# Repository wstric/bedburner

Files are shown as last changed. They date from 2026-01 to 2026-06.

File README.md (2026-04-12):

# PTC Heated bed fans mod for Voron 2.4 Printers
Spicy _bed_ fan mod with an "after _burner_" -> BedBurner.

Installed on Voron 2.4 bed rails. Can be placed on the outside, center or both.

Outer placement will be covered by the bed for 300 and 350 size but exposed on 250 size.

Requires raising the bed for clearance and to prevent damage to the bed heater.
Mods like Whoppingpochard kinematic bed mount do this with other benefits.

:fire: :fire: :fire:

> [!CAUTION]
> Installation of this mod involves wiring mains AC voltage and addition of heaters without thermistor feedback.
>
> Careful wiring and component selection can reduce the risk of injury or fire,
> but only similar to the existing components of a v2.4 but never zero.
>
> This mod should not be attempted without experience and caution.
> I am not responsible for any resulting damage or harm.

> [!Warning]
> Do NOT ask about this mod in the Voron Design Discord.

:fire: :fire: :fire:

## Design

The goal of this mod was to create a minium height chamber heater for the Voron V2.4 that
could slip into the unused space under the bed and provide enough thermal output to match
the extruder. This would allow the printer to more easily heatsoak at the same temperatures
that would be reached during printing. More active chamber temperature control was a bonus
and a slight increase in temperatures was welcome. Other heaters setups can be off-the-shelf
and more off-the-shelf and provide much more power. However, they were simply too bulky
and had to mounted in the open or be in the way of existing components.

After much research and trying to make hotend cartridge heater work I found the aluminum shell
PTC heater form factor. While lacking in surface area it is very compact, electrically isolated
and could be easily mounted heatsink. Balancing space, thermal out, and availability lead to
35mm x 20mm x 5mm nominal size PTC and 50mm x 50mm x 20mm heatsink. This left enough space for
safety features such as a thermal switch as a fail safe and further cap the maximum temperature.

Modifying the off the shelf heatsink ending up being one of the most challenging part. While
the steel brackets (metal for safety in the worst case, and steel for poor conductivity) would
have been impossible to make myself they were easy to outsource to services like SendCutSend.
The modified heatsink would have been prohibitive to outsource machined from raw stock and
a struggle to do with hand tools. There were easier ways to mount but was decided that retaining
components in pockets strapped in with screws was necessary for safety.

The resulting setup ended being a little too tall for a stock V2.4 bed spacers. This wasn't an
issue since the Whooping kinematic bed mod already gave plenty of height. Using 5015 radial
blower fan and matching ducts; two units could be fit in between the bed extrusions and
another two could be hidden under a 300mm or 350mm bed on the outside.

### Results
* Twin BedBurner test rig setup:
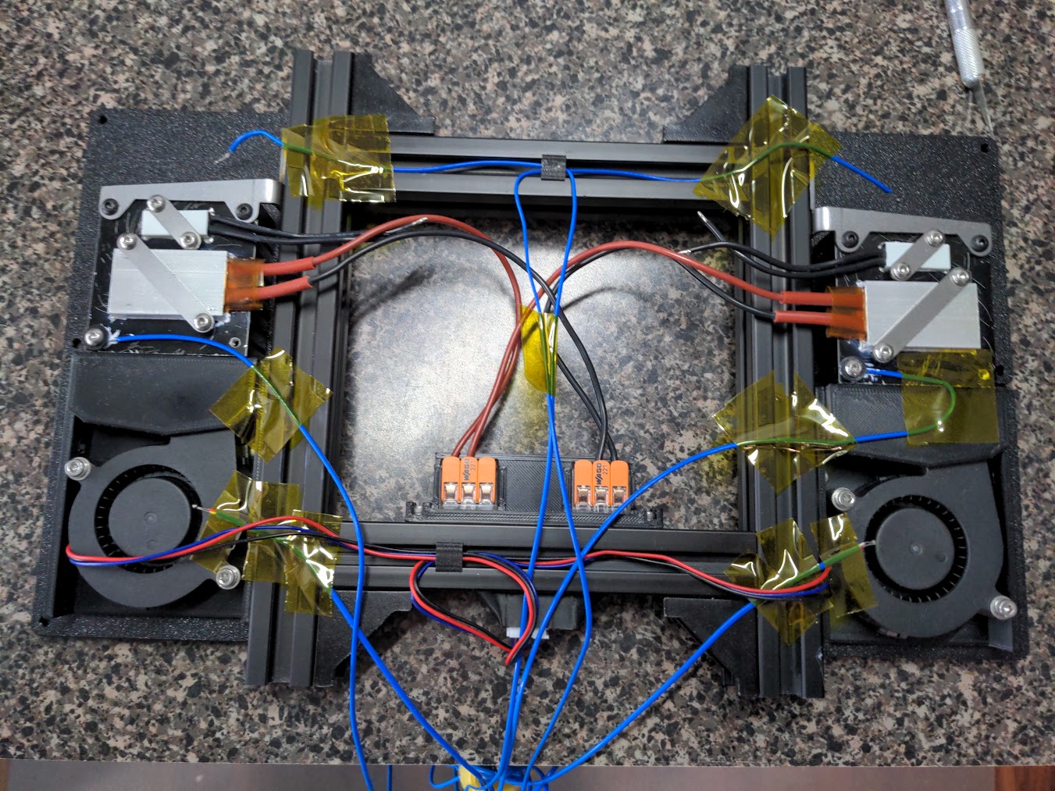
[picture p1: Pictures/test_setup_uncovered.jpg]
test_setup_uncovered
  * 
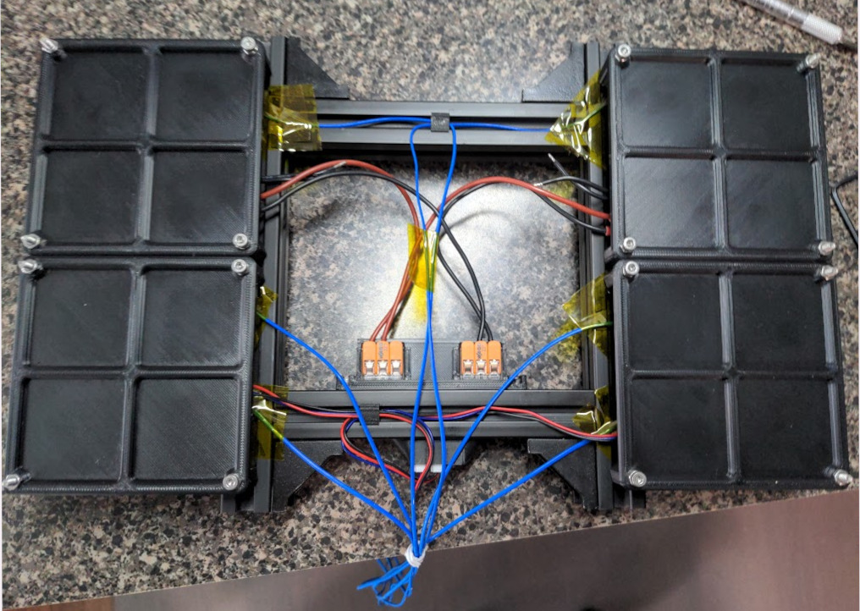
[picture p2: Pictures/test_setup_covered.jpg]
  * 
  * Thermocouples were placed at the fan intake, on the block surface and at the block exhaust.
  * Combined amperage was measured and recorded along with temperature readings.
  * was inside an thinly insulated box with a simulated V2.4 configuration.
  * Heaters output over 70 watts each at 25C ambient.
  * The block surface peaked at rough 80C in 25C ambient.
  * Output dropped to roughly 60 watts each at 75C ambient.
* Twin BedBurner setup installed in a v2.4 300:
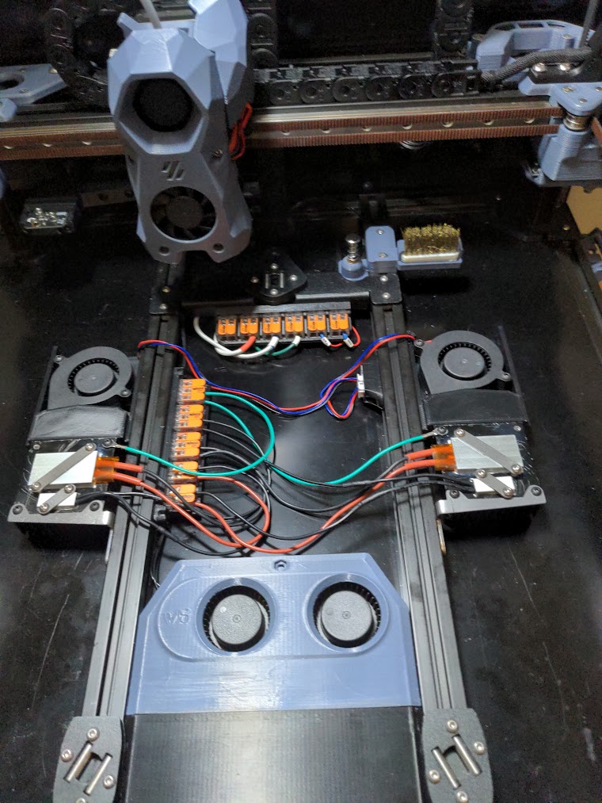
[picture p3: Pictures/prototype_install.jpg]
prototype_install
  * 
  * Stock panels and doors, stock exhaust, no blanket or insulation.
  * Nevermore micro v6 recirculating and exaust fan off.
  * Heatsoaking bed at 105C and 100% BedBurner.
  * Chamber temperature reached stable 65C. 
  * Measured at gantry rear extrusion with toolhead centered and 120mm over bed

## Parts List
* Machined heater block
* Cut and bent bracket and straps
* PTC heater
* thermal failsafe (thermal switch / thermal fuse / thermistor)
* 5015 radial (blower) fan
* 3D printed fan duct
* Assorted M3 hardware

### [Detailed BOM](./README_bom.md)

## Instructions

### [Fabrication](./README_fabrication.md)

### [Assembly](./README_assembly.md)

### [Configuration](./README_config.md)

---

Special thanks to the Fabreeko discord and Delmar for tolerating these shenanigans.

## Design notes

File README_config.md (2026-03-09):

# BedBurner Software Configuration

Klipper does not make chamber heaters easy.
They are, in effect, modeled as bed heaters which causes complications in most configurations.
The two main paths for configuring are to work around the Klipper or implement custom control.

## Klipper Control Solution

Klipper control gets hacky, but has the advantage of being controlled in real time.
It is always running and will not be blocked by the command queue.
The macro is also much easier to understand even if what is can do is narrow.
The only real downside it you are working around the limitations and opinions of Klipper.
Depending on your setup this might be no downside at all.

Some limitations you might need to work around include:
  * Heaters can only be controlled by a temperature sensor
  * Using verify_heater is impossible using the chamber temp. No safety for you.
  * Nether heater_fan or controller_fan can cycle off except during cool down.
  * If you have one chamber termistor, duplicate pin validation.

Provided example was extensively tested in Kalico v0.12 and provides control of
chamber heater & fan, filter and exhaust.

#### [klipper control example config](/Firmware/klipper/klipper_control)

## Custom Control Solution
Custom control gives a lot of freedom to customize how it behaves.
I have implemented my own version using delayed_gcode which makes it simple to implement,
but comes with the limitation that it can be interrupted temporally by long running commands
(like a typical print start macro).

The configuration is simple configuration and can model the filter, exhaust, heater fan
and heater element as `fan_generic` so that a macro may control without Klipper stepping in.
Practically, you are limited to watermark (aka bang-bang) control in a custom macro,
but this is quite suitable for chamber temperature regulation.

Provided example was extensively tested in Klipper v0.12 and provides control of
chamber heater & fan, filter and exhaust.

#### [custom control example config](/Firmware/klipper/custom_control)

---

For examples given above chamber temperature control is abstracted by `HEAT_CHAMBER` and `COOL_CHAMBER` macros.
The `HEAT_CHAMBER` should be called in your print start (and heatsoak if you have one) macros.
`COOL_CHAMBER` should be called in your print end macro.

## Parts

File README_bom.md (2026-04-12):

# BedBurner Detailed BOM

## Common Components 
* Heater block
  * Heatsink - 50mm x 50mm x 20mm
  * Machined with component pockets and tapped holes
  * Variant of block should match the thermal fail-safe option selected
  * Detailed instructions in [fabrication section](./README_fabrication.md#Heater-Heatsink)

* Mouting bracket
  * Cut and bend from 16ga mild steel
  * Requires front, rear or both brackets
    * Rear bracket least compact but accessible screws makes easier to install and service
    * Front bracket covers extrusion screws and makes hard to align
    * Can use both front and rear brackets for extra sturdy mounting
  * STEP models and DXF files are provided
  * Detailed instructions in [fabrication section](./README_fabrication.md#Heater-Bracket)

* PTC heater
  * Aluminum shell PTC heater
  * Nominal size 35mm x 20mm x 5mm size
  * Quality control is loose so test current draw and max temp before usage

* PTC component strap
  * Cut from 22ga mild steel
  * Detailed instructions in [fabrication section](./README_fabrication.md#Component-Straps)

* 5015 radial (blower) fan
  * Recommended to use fans rated for high performance and chamber temperatures

* Fan duct
  * [STLs](/STL/fan_duct) provided
  * Typical voron print settings
    * ABS/ASA, 0.4mm extrusion, 0.2mm layer, 4 wall, etc.
  * 2 x printed screw diam spacers are optional

* 2 x M3, 8mm BHCS/SHCS - for PTC strap
* 2 x M3, 6mm BHCS/SHCS - for bracket to extrusion (per bracket)
* 2 x M3, 4mm BHCS/SHCS - for block to bracket (per bracket)
* 2 x M3, 18mm BHCS/SHCS - for fan to duct
  * Not a common size
  * Cut down longer screws if needed
* 1 x M3, 8mm BHCS/SHCS - for duct to extrusion
* 2 x 2020 M3 t-nuts (twist-in or roll-in preferred) (per bracket)

* 2 x short M3 heatset insert (M3 x 4.6mm x 3mm)
  * not common but [CNC Kitchen](https://cnckitchenus.store/products/heat-set-insert-m3-x-3-short-version-100-pieces) makes them

* One thermal safety option
  * Not recommended to rely on PTC maximum temperature in case of failure
  * Thermal fail-safe options provided below with required BOM

* Optional thermal paste/grease
  * use to improve conductivity between PTC shell or thermal switch/fuse and heater block
  * operation temperature should be higher than PTC or thermal switch/fuse rating

## Thermal Switch Option

* (Use ptc_tswitch variant block)

* Thermal switch
  * KSD9700 insulated bimetal temperature/thermostat switch
  * Recommended 120C Normally Closed
  * Quality control is loose so test trigger temp before usage

* TSwitch component strap
  * Cut from 22ga mild steel.
  * Detailed instructions in [fabrication section](./README_fabrication.md#Component-Straps)

* 2 x M3, 8mm BHCS/SHCS - for tswitch strap

## Thermal Fuse Option

* (Use ptc_tfuse variant block)

* Thermal fuse
  * RH series ceramic thermal cut-off fuse
  * Commonly used as a fail-safe for voron bed heaters
  * Recommended 125C 10A 250V rating

* 1 x M3, 8mm FHCS - for tfuse.
  * SHCS and BHCS can also work but might need a washer

## Thermistor Option

* (Recommended ptc_tfuse variant block)

* M3 hex screw thermistor
  * 3mm length of M3 x 0.5mm screw thread
  * Typically 100K 3950 or 104GT-2

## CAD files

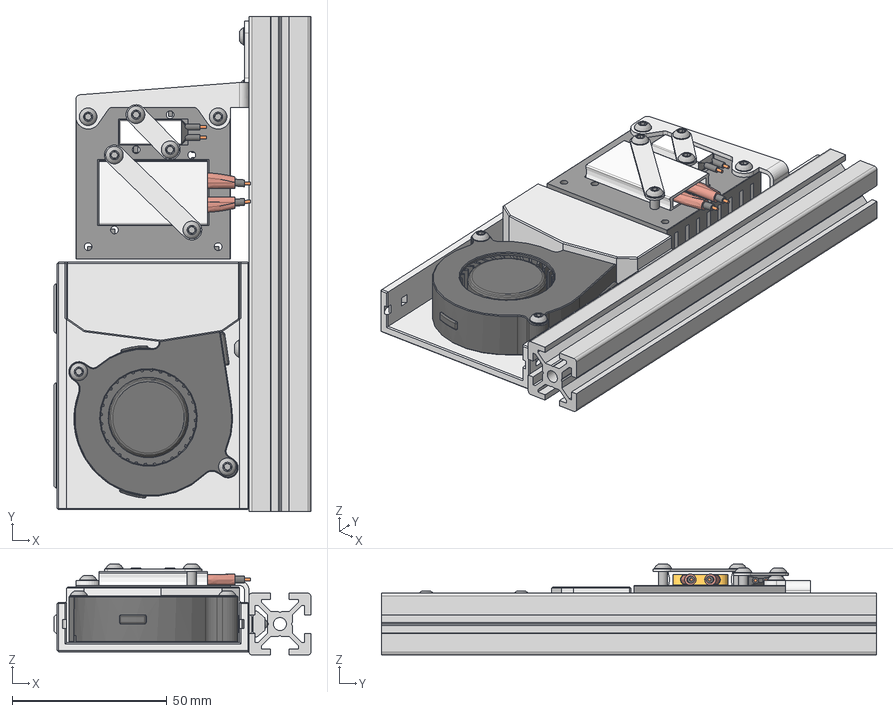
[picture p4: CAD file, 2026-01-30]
CAD/bedburner-assembly.step
83.0 x 160.0 x 29.4 mm
HFS5-2020-160
tnut_2020_m3_roll x 3
heater_heatsink_ptc_tswitch
ptc_mini_element_v1
thermal_switch_ksd9700_v1
heater_strap_ptc
heater_strap_tswitch
m3x8_bhcs x 5
heater_fan_duct
heater_fan_screw_spacer x 2
heatset_m3_short_cnck x 2
fan_radial_50x15
m3x18_bhcs x 2
heater_bracket
m3x6_bhcs x 2
m3x4_bhcs x 2

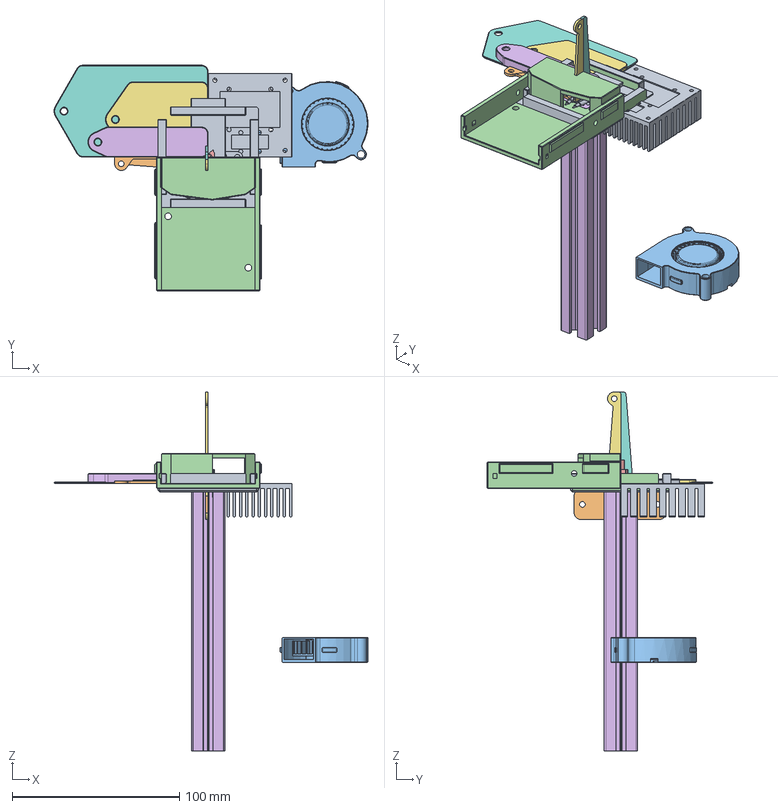
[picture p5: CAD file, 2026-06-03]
CAD/bedburner.FCStd
187.8 x 135.0 x 214.8 mm
heater_strap_ptc
heater_rear_bracket
heater_strap_tswitch
heater_fan_duct
heater_fan_screw_spacer
spacer_block_frame
spacer_block_deck
spacer_duct_deck
heater_heatsink_ptc_tswitch
heater_front_bracket
heater_heatsink_ptc_tfuse
heater_heatsink_drill_guide_ptc_labeled
heater_heatsink_drill_guide_tswitch_labeled
heater_heatsink_drill_guide_tfuse_labeled
heater_heatsink_template_ptc_1-16_labeled
heater_heatsink_template_ptc_1-8_labeled
heater_heatsink_template_tswitch_1-16_labeled
heater_heatsink_template_tswitch_1-8_labeled
heater_heatsink_template_tfuse_1-16_labeled
heater_heatsink_template_tfuse_1-8_labeled
heatset_m3_short_cnck
m3x4_bhcs
m3x6_bhcs
m3x8_bhcs
ptc_mini_element_v1
thermal_switch_ksd9700_v1
fan_radial_50x15
m3x18_bhcs
tnut_2020_m3_roll
HFS5-2020-160
heater_front_bracket_unfold
heater_rear_bracket_unfold

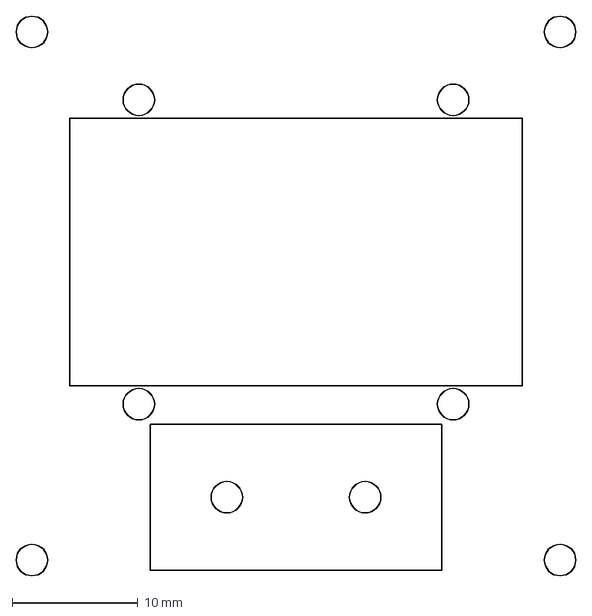
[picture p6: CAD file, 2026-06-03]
Drawing/block/bedburner-block_ptc_tfuse.dxf
44.5 x 44.5 mm

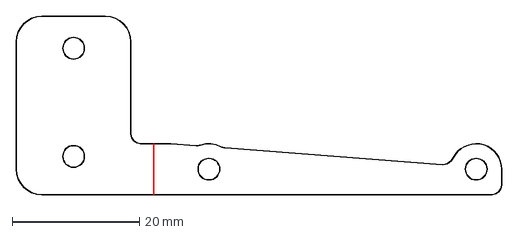
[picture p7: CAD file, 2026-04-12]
Drawing/bracket/bedburner-bracket_front.dxf
76.3 x 28.0 mm

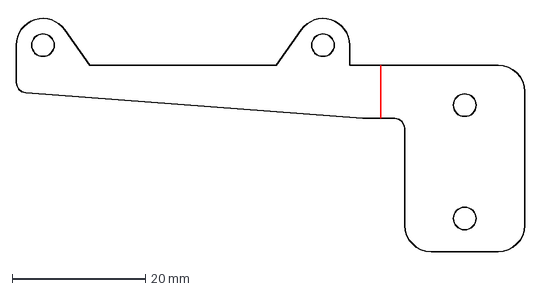
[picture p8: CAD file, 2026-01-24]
Drawing/brackets/block_bracket_mildsteel16ga_mirror.dxf
76.3 x 35.3 mm

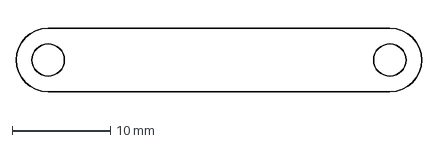
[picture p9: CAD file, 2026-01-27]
Drawing/strap/bedburner-strap_ptc.dxf
41.3 x 6.50 mm

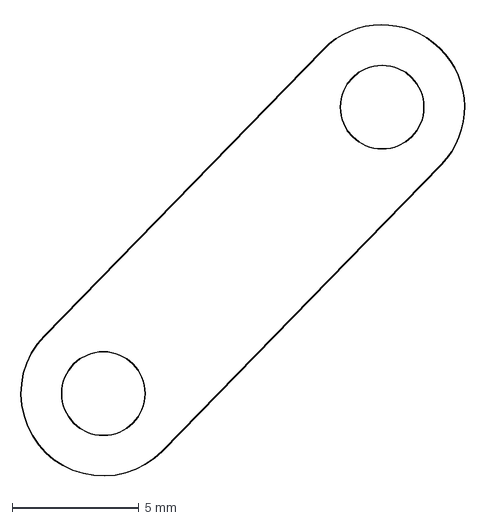
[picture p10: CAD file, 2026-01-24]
Drawing/straps/heater_strap_tswitch.dxf
18.0 x 18.3 mm

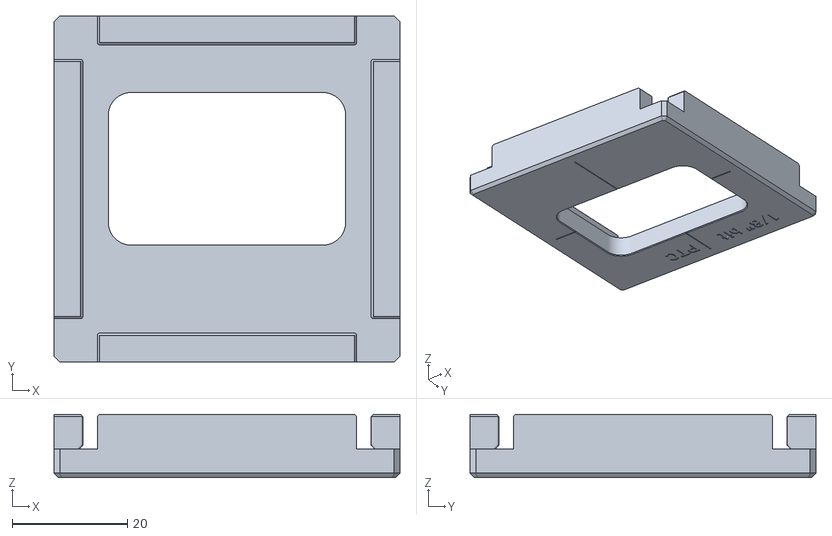
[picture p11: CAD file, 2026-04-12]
STL/block_template/block_router_template_ptc_1-8.stl
60.0 x 60.0 x 11.0

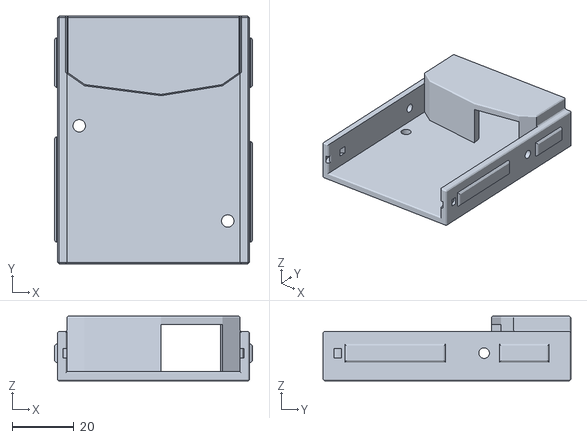
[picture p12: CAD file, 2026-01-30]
STL/fan_duct/fan_duct.stl
64.0 x 80.0 x 21.0

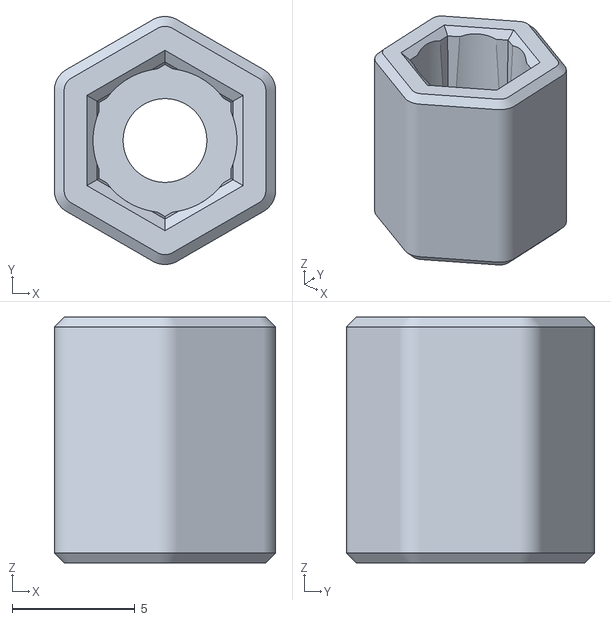
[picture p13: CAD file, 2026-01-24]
STL/test/test_rig-spacer_foot.stl
9.00 x 10.1 x 10.0

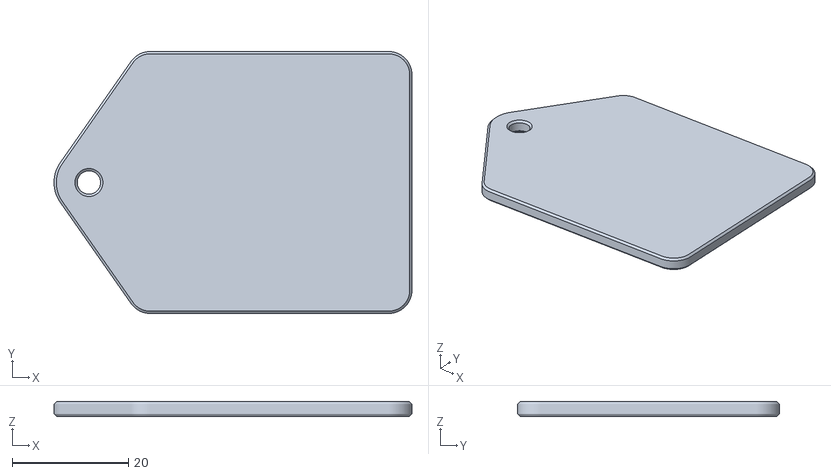
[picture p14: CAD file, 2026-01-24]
STL/tools/install_spacer-block_deck.stl
61.5 x 45.0 x 2.50

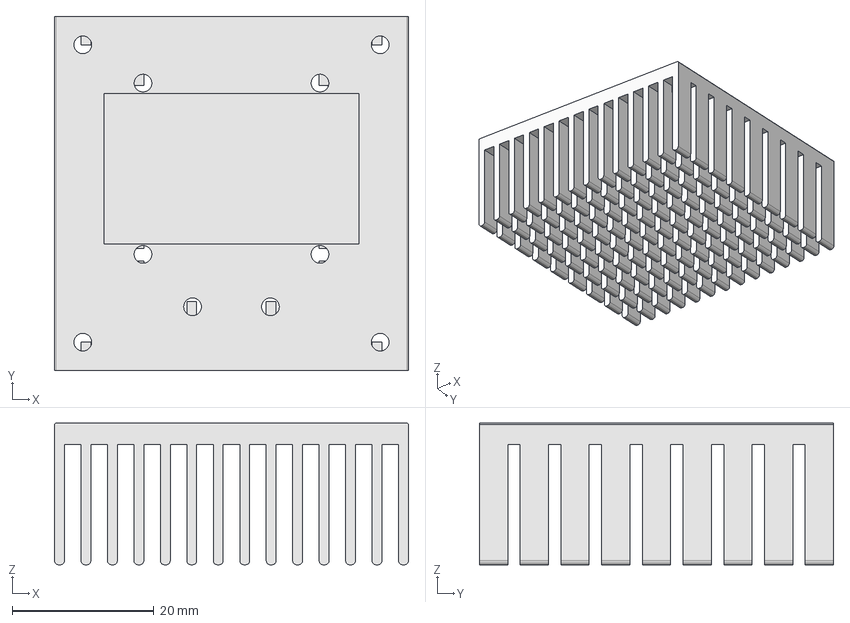
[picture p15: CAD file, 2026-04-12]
CAD/bedburner-block_ptc_tfuse_no-pocket.step
50.0 x 50.0 x 20.0 mm

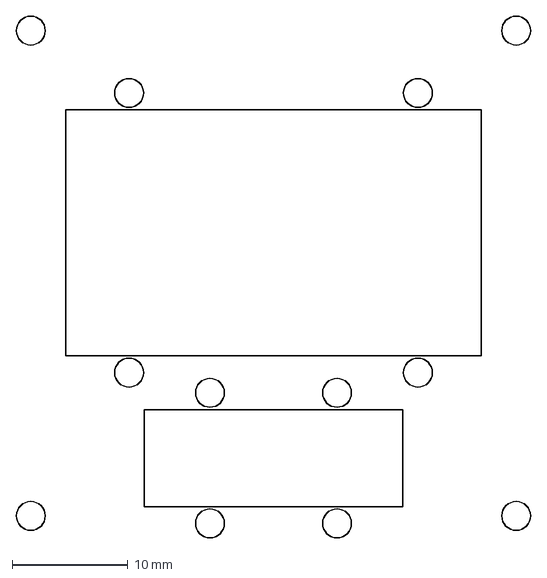
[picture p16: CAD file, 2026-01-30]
Drawing/block/bedburner-block_ptc_tswitch.dxf
44.5 x 45.1 mm

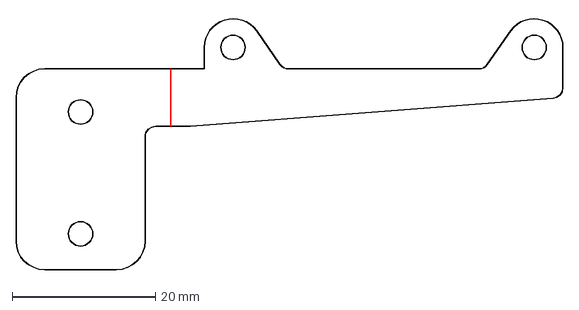
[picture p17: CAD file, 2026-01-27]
Drawing/bracket/bedburner-bracket_rear.dxf
76.3 x 35.3 mm

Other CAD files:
Drawing/strap/bedburner-strap_tswitch.dxf
Drawing/straps/heater_strap_ptc.dxf
STL/block_template/block_router_template_tswitch_1-16.stl
STL/test/test_rig-spacer_deck.stl
CAD/bedburner-block_ptc_tfuse.step
CAD/bedburner-block_ptc_tswitch.step
CAD/bedburner-bracket_front.step
CAD/bedburner-bracket_rear.step
CAD/bedburner-heater_fan_duct.step
CAD/test_jig.FCStd
STL/block_template/block_drill_guide_tfuse.stl
STL/block_template/block_drill_guide_tswitch.stl
STL/block_template/block_router_template_ptc_1-16.stl
STL/block_template/block_router_template_tfuse_1-16.stl
STL/block_template/block_router_template_tfuse_1-8.stl
STL/block_template/block_router_template_tswitch_1-8.stl
STL/fan_duct/fan_screw_spacer_x2.stl
STL/test/test_rig-duct_cover.stl
STL/test/test_rig-spacer_extrusion.stl
STL/tools/install_spacer-block_frame.stl
STL/tools/install_spacer-duct_deck.stl

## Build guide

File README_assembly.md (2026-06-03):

# BedBurner Assembly Instructions

## CAD Reference
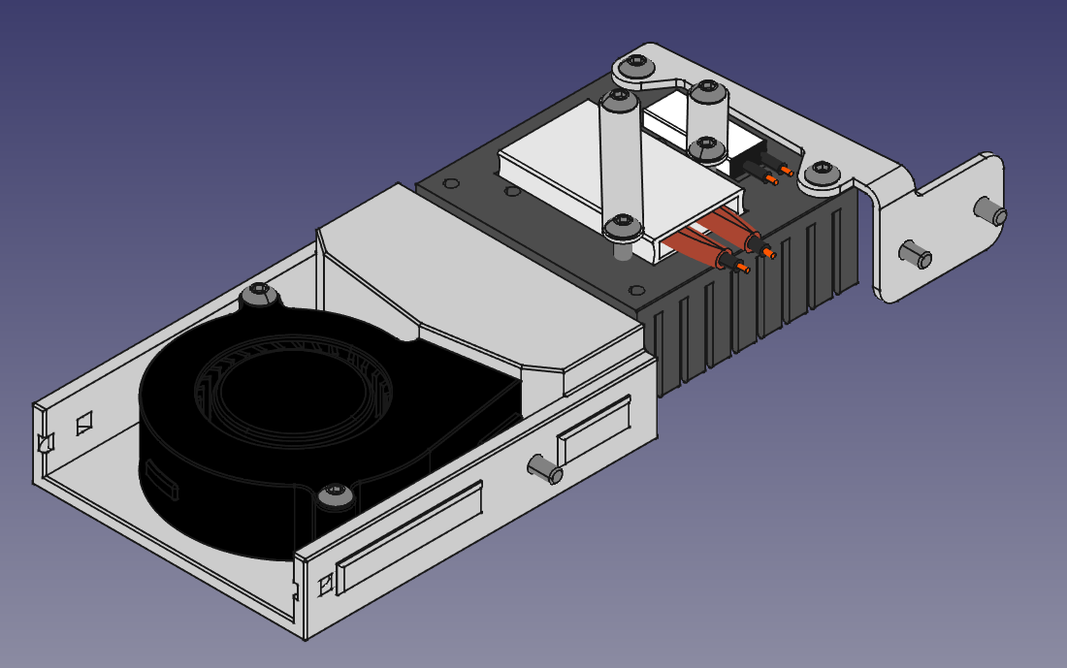
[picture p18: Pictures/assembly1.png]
CAD Assembly 1

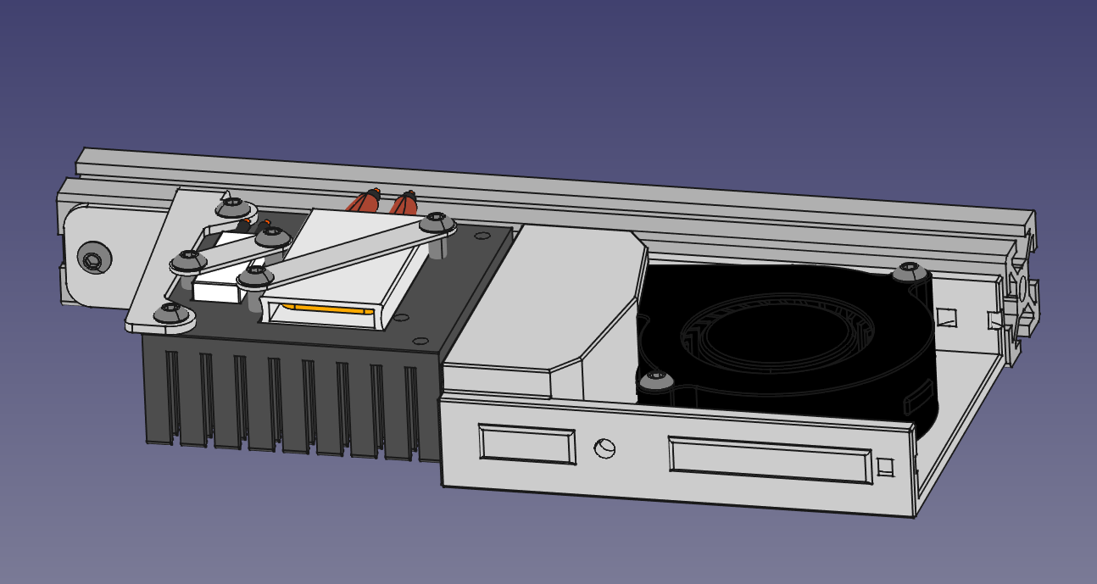
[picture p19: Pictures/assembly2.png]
CAD Assembly 2


## Wiring Disclaimer

This document will not go into wiring details because that is a topic I don't
feel comfortable speaking to. I will just repeat some general 3D printer
electrical safety recommendations.
 * Make sure mains components are fuse protected and properly grounded.
 * Any heater, including PTC heaters, should have some thermal protection
such as a thermal switch, thermal fuse or thermistor under firmware control.
 * You should know the current draw of components being used and plan accordingly.
 * Adequate thickness wire should be used for the expected current and temperature.

## Heater Heatsink

Steps will vary slightly based on choice of components.
1. Place PTC heater into large heatsink pocket.
   * add temperature rated thermal grease if desired.
2. Place PTC strap diagonally across the PTC and secure with two M3 x 8mm screws.
3. Install thermal safefy component.
    * Thermal Switch / Thermal Fuse:
      1. Place thermal switch body into the smaller heatsink pocket
          * recommended to orient wires facing the same side as the PTC heater
          * add temperature rated thermal grease if desired.
      2. Place thermal switch strap diagonally across the thermal switch and secure with two M3 x 8mm screws.
    * Thermal Fuse:
      1. Place thermal switch body into the smaller heatsink pocket
          * recommended to orient wires facing the same side as the PTC heater
          * add temperature rated thermal grease if desired.
      2. Secure thermal fuse to heatsink with one M3 x 8mm screw through mouting hole
    * Thermistor:
      1. Thread Thermistor into any unused threaded holes in the heatsink.
          * recommended to use central but accessible holes like those for thermal fuse mounting.

## Fan Duct

1. Press short M3 heatset inserts for fan mounting into holes printed part
2. Attach the 5015 blower fan to the duct base using M3 x 18mm screws
3. Secure fan wire using a cable tie on one side of the fan duct
   * use the side that makes sense for cable management when it is installed.
   * you will probably want to make mirrored pairs.

## Installation

1. Loosely attach Heatsink Bracket(s) to bed frame extrusion using two M3 x 6mm screws and two tnuts each
   * if using roll-in tnuts they should face orient so they do not interfere.
   * pay attention to which bracket you are using because it will decide the direction of airflow.
   * rear style bracket screws can be loosened and slid into final position later.
   * front type bracket screws can not be accessed later so position will be final.
2. Loosely attach heatsink unit to bracket(s) with M3 x 4mm screws.
   * heatsink fins should be oriented parallel to extrusion.
   * hole tolerance is generous to allow for fabrication inaccuracies.
   * use [printed spacers](/STL/tools) space block properly off deck and extrusion.
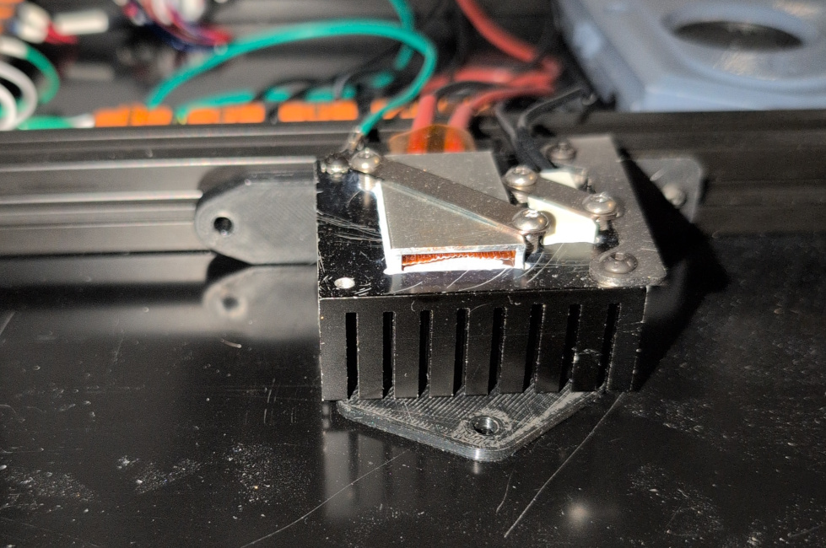
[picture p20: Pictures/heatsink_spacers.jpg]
Heater Heatsink Spacers
   
3. Tighten screws to secure heatsink into position.
4. Loosely attach Fan Duct to bed frame extrusion using one M3 x 6mm screw and tnuts.
   * Duct opening should face toward the heatsink.
   * You may find it easier to reach the screw by temporarily detaching the 5015 fan.
5. Slide Fan Duct until there is a small gap between heatsink then tighten to secure.

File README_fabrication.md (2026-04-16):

# BedBurner Fabrication Instructions

## Heater Heatsink

Starting with a commodity aluminum 50mm x 50mm x 20mm heatsink.
These often come with thermal tape preapplied which will need to be removed.

Variants are provided for thermal switch, thermal fuse or thermistor
fail-safe options are given.

Symmetrical screw holes are modeled but only about half are necessary.
One could save some wear on your bits/taps if you machine the ones needed
for each block.

Similarly, the thermal fuse pocket is not as necessary for secure mounting as
those for the PTC and thermal switch so it can be skipped if desired.

Technical drawings are provided for clarity in [/Drawing/block](/Drawing/block).

### CNC Mill (Recommended)

It is unlikely to be cost effective have the block machined from raw stock and
commercial services are unlikely start from a purchased heatsink.
The best option if you have a CNC mill or "a friend with a CNC mill".

CAM results were very good drilling, thread milling and then making the pockets with a 3mm end mill.
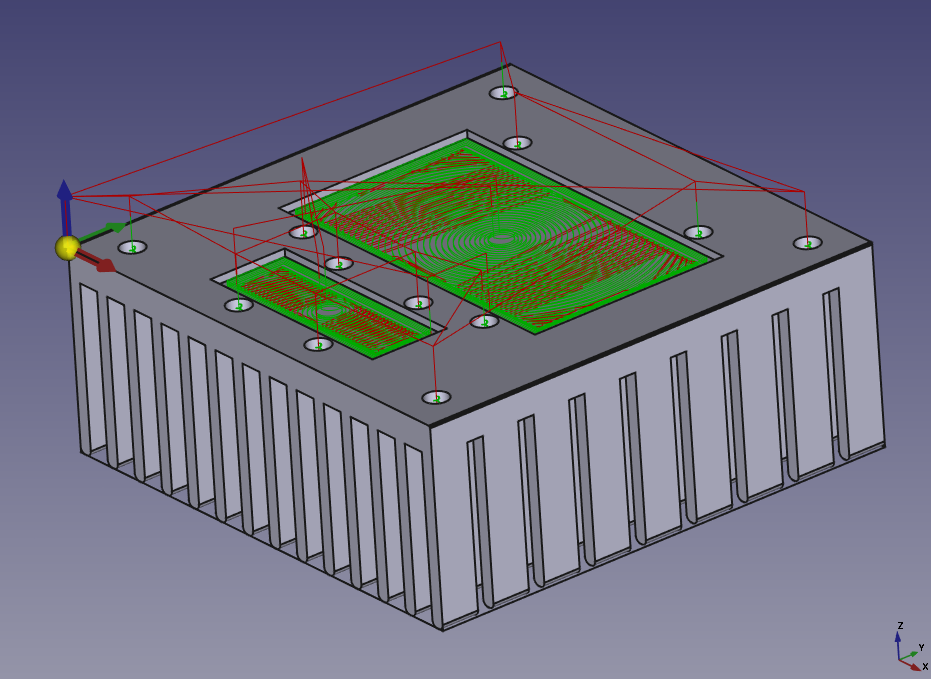
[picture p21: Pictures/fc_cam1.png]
Freecad CAM project


Files are provided as [STEP](/CAD) or [DXF](/Drawing/block).

### Hand Tools

The prototype unit blocks were made with hand tools and it can be done if you
have the resolve.

3D printable [guides and templates](/STL/block_template) are provided to use with
hand drills and trim routers. The guides and templates fit snugly onto the sides of
the heatsink.

Drill guide uses 2.0mm bit. Step up to 2.5mm bit for M3 tap.
Have multiple drill bits and end taps. You will likely break multiple.
Drill/tap depth should be approximately 4.5mm.

The router templates requires a 5/16" OD Router bushing. A 1/16th inch bit is necessary
to get corner relief. Templates to use A 1/8th inch bit are also provided to quickly hog
out material and just let the smaller bit clean up the edges and corners.

> [!CAUTION]
> Carbide trim router bits can cut aluminum very well but doing so requires skill and
> setup to do so safely. Do not attempt if you do not have experience using this tool.

## Heater Bracket

Cut and bent from plain 16ga mild steel these parts are straight forward to source.
This really makes sense to outsource to laser cutting services. The prototype units
were ordered from SendCutSend. At the time, a set of parts wouldn't get to the
minimum order amount.

Mirror pairs can be made using the same file by bend up and bend down.

Files are provided as [STEP](/CAD) or [DXF](/Drawing/bracket).

Technical drawings are provided for clarity in [/Drawing/block](/Drawing/bracket).

## Component Straps

These are very simple parts made plain 22ga steel and can me made by hand if
desired but I would just include them in the order for the heater brackets.

Separate files are provided for shorter thermal switch and longer ptc straps.

Only [DXF](/Drawing/strap) files are provided.

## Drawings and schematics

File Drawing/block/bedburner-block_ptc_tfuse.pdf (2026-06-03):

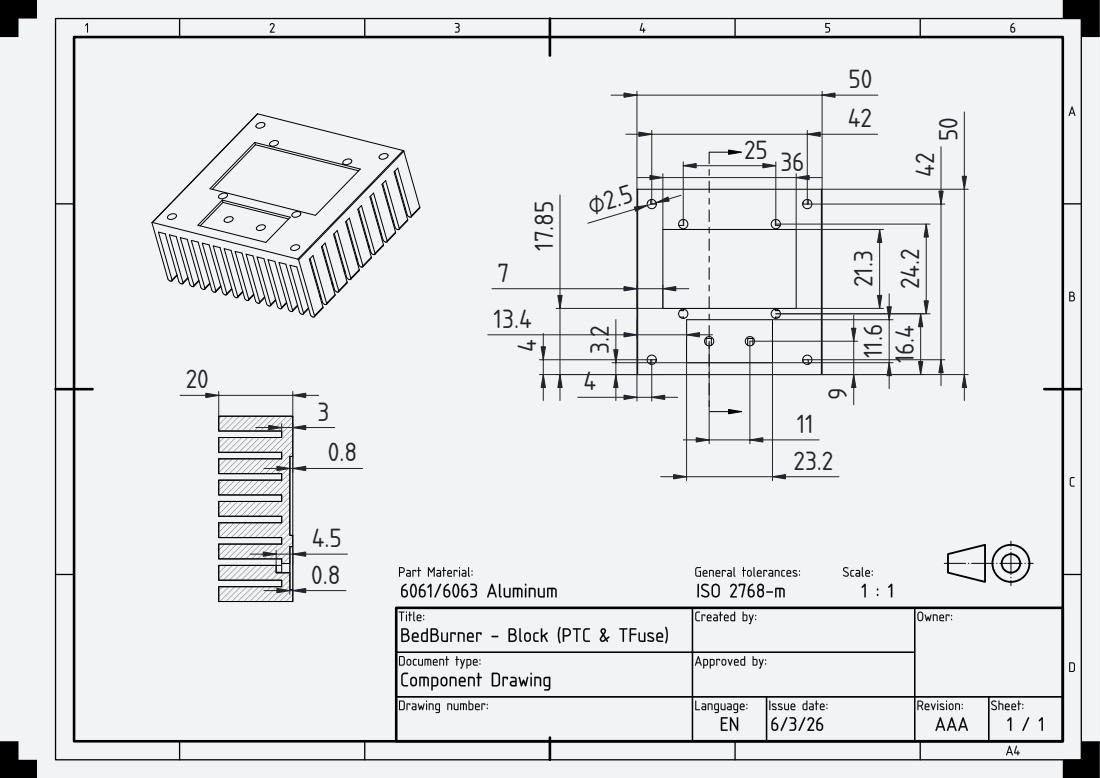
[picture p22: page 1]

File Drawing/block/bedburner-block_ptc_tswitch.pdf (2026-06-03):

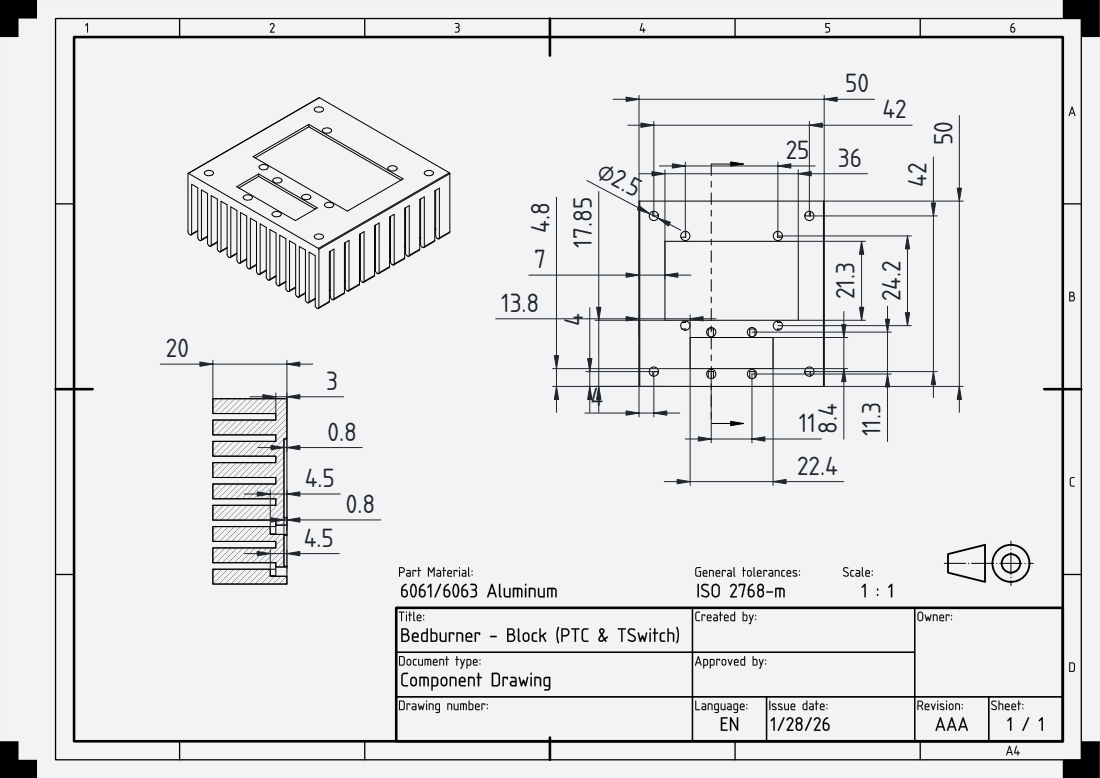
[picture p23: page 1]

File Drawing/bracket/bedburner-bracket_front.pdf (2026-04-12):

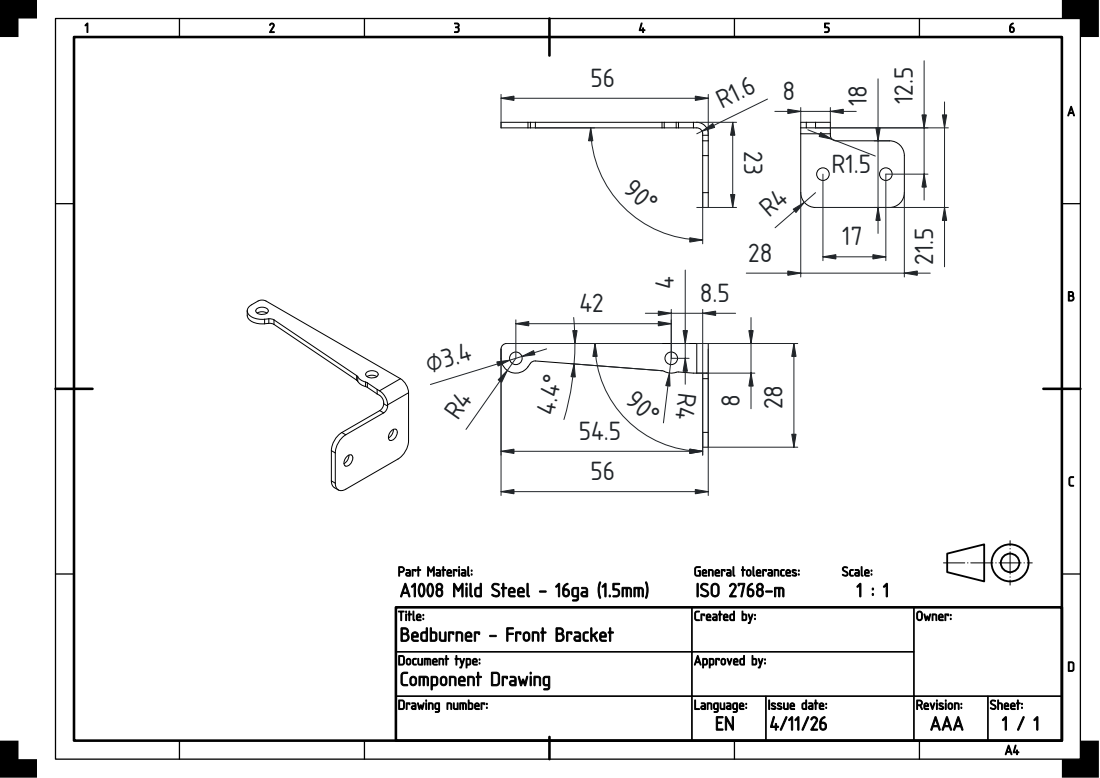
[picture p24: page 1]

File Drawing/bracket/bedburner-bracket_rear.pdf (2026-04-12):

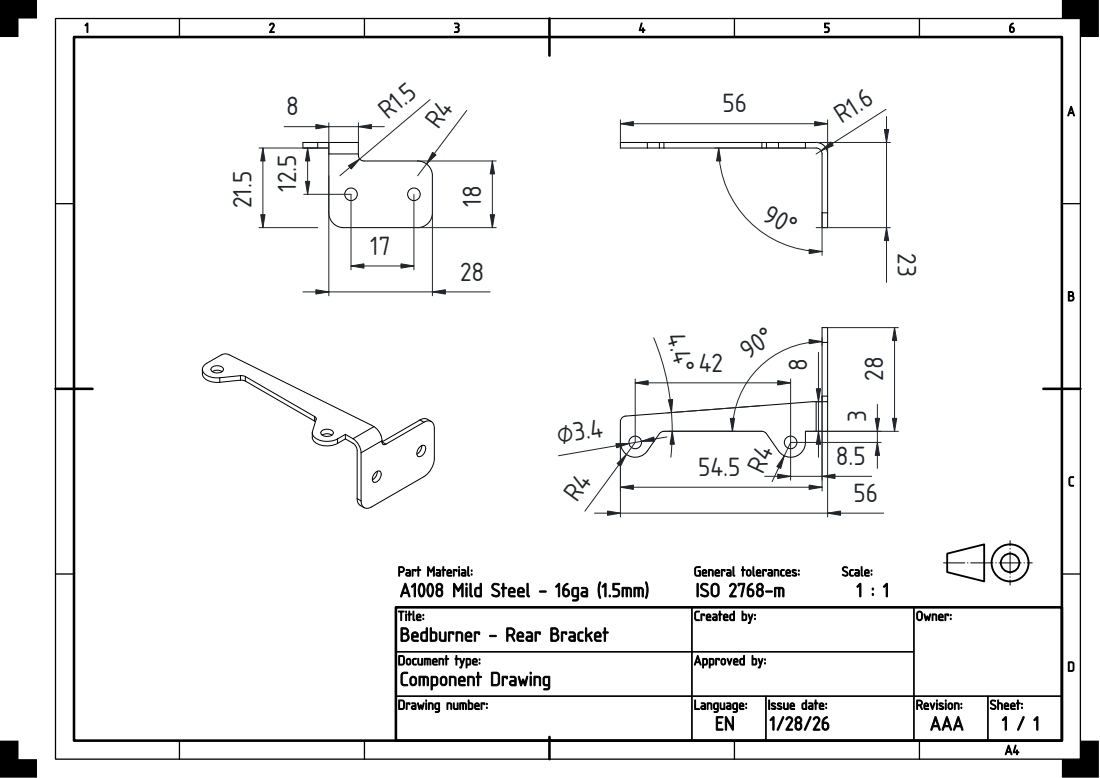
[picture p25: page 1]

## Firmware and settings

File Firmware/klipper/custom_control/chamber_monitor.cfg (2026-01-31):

#####################################################################
#   Macros - Chamber Monitor
#####################################################################

[gcode_macro HEAT_CHAMBER]
description: prompts chamber monitor to heat chamber and hold at target temperature

## constants
variable_chamber_threshold:      35.5 # in celsius
variable_chamber_trigger_under:   0.5 # in celsius
variable_chamber_trigger_over:    1.0 # in celsius
variable_nevermore_threshold:    40.0 # in celsius
variable_check_interval:         10   # in seconds
variable_burner_fan_delay:       30   # in seconds

## control variables
variable_stage: None # heating -> cooling -> None;
variable_target_temp:       0
variable_trigger_nevermore: 0
variable_trigger_bedburner: 0
variable_trigger_exhaust:   0
variable_burner_cooldown:   0

gcode:
    {% set TARGET = params.TARGET | default(0) | float %}
    {% if TARGET > chamber_threshold %}
        # set mode and triggers
        SET_GCODE_VARIABLE MACRO=HEAT_CHAMBER VARIABLE=stage VALUE="'heating'"
        SET_GCODE_VARIABLE MACRO=HEAT_CHAMBER VARIABLE=target_temp       VALUE={ TARGET }
        SET_GCODE_VARIABLE MACRO=HEAT_CHAMBER VARIABLE=trigger_nevermore VALUE={ nevermore_threshold }
        SET_GCODE_VARIABLE MACRO=HEAT_CHAMBER VARIABLE=trigger_bedburner VALUE={ TARGET - chamber_trigger_under }
        SET_GCODE_VARIABLE MACRO=HEAT_CHAMBER VARIABLE=trigger_exhaust   VALUE={ TARGET + chamber_trigger_over }
        SET_GCODE_VARIABLE MACRO=HEAT_CHAMBER VARIABLE=burner_cooldown   VALUE=0
        # kick off monitor
        m118 Chamber Monitor - Heating -> { TARGET }C
        UPDATE_DELAYED_GCODE ID=chamber_monitor DURATION=1
    {% else %}
        # clear out mode and triggers
        SET_GCODE_VARIABLE MACRO=HEAT_CHAMBER VARIABLE=stage VALUE="'None'"
        SET_GCODE_VARIABLE MACRO=HEAT_CHAMBER VARIABLE=trigger_nevermore VALUE=0
        SET_GCODE_VARIABLE MACRO=HEAT_CHAMBER VARIABLE=trigger_bedburner VALUE=0
        SET_GCODE_VARIABLE MACRO=HEAT_CHAMBER VARIABLE=trigger_exhaust   VALUE=0
        SET_GCODE_VARIABLE MACRO=HEAT_CHAMBER VARIABLE=burner_cooldown   VALUE=0
    {% endif %}


[gcode_macro COOL_CHAMBER]
description: prompts chamber monitor to let chamber cool
gcode:
    {% if printer['gcode_macro HEAT_CHAMBER'].stage == "heating" %}
        # set mode to cooling; assume monitor already looping
        m118 Chamber Monitor - Cooling
        SET_GCODE_VARIABLE MACRO=HEAT_CHAMBER VARIABLE=stage VALUE="'cooling'"
    {% elif printer['gcode_macro HEAT_CHAMBER'].stage == "cooling" %}
        m118 Chamber Monitor - Already Cooling
    {% else %}
        # NOOP
        m118 Chamber Monitor - None
        SET_GCODE_VARIABLE MACRO=HEAT_CHAMBER VARIABLE=stage VALUE="'None'"
    {% endif %}


[delayed_gcode chamber_monitor]
gcode:
    # macro state
    {% set heat_chamber = printer['gcode_macro HEAT_CHAMBER'] %}
    {% set stage             = heat_chamber.stage %}
    {% set target_temp       = heat_chamber.target_temp %}
    {% set trigger_nevermore = heat_chamber.trigger_nevermore %}
    {% set trigger_bedburner = heat_chamber.trigger_bedburner %}
    {% set trigger_exhaust   = heat_chamber.trigger_exhaust %}
    {% set burner_cooldown   = heat_chamber.burner_cooldown %}
    # hardware state
    {% set chamberTemp     = printer["temperature_sensor chamber"].temperature %}
    {% set en_nevermore    = printer["fan_generic nevermore"].speed > 0 %}
    {% set en_burnerHeater = printer["fan_generic burnerHeater"].speed > 0 %}
    {% set en_burnerFan    = printer["fan_generic burnerFan"].speed > 0 %}
    {% set en_exhaust      = printer["fan_generic exhaust"].speed > 0 %}

    ### mode is heating
    {% if stage == "heating" %}
        ## handle nevermore - heating
        {% if not en_nevermore and trigger_nevermore > 0 %}
            # nevermore is off turn it on
            SET_FAN_SPEED FAN=nevermore SPEED=1
        {% endif %}
        ## handle burner - heating
        {% if not en_burnerHeater and trigger_bedburner > 0 and chamberTemp < trigger_bedburner %}
            # burner off and below trigger; turn on w/fan
            SET_FAN_SPEED FAN=burnerHeater SPEED=1
            SET_FAN_SPEED FAN=burnerFan SPEED=1
            SET_GCODE_VARIABLE MACRO=HEAT_CHAMBER VARIABLE=burner_cooldown VALUE={ heat_chamber.burner_fan_delay }
        {% elif en_burnerHeater and chamberTemp > target_temp %}
            # burner on and above target; turn off
            SET_FAN_SPEED FAN=burnerHeater SPEED=0
        {% endif %}
        ## handle exhaust - heating
        {% if not en_exhaust and trigger_exhaust > 0 and chamberTemp > trigger_exhaust %}
            # exhaust is off and above trigger; turn on
            SET_FAN_SPEED FAN=exhaust SPEED=1
        {% elif en_exhaust and chamberTemp < target_temp %}
            # exhaust is on and below target; turn off
            SET_FAN_SPEED FAN=exhaust SPEED=0
        {% endif %}
    {% endif %}

    ### mode is cooling
    {% if stage == "cooling" %}
        # dwell for 1ms to prevent from going idle
        G4 P1
        # clear burner target if set
        {% if trigger_bedburner > 0 %}
            SET_GCODE_VARIABLE MACRO=HEAT_CHAMBER VARIABLE=trigger_bedburner VALUE=0
        {% endif %}
        # clear exhaust trigger if below target
        {% if trigger_exhaust > 0 and chamberTemp < target_temp %}
            SET_GCODE_VARIABLE MACRO=HEAT_CHAMBER VARIABLE=trigger_exhaust VALUE=0
        {% endif %}

        ## handle nevermore - cooling
        {% if not en_nevermore and trigger_nevermore > 0 and chamberTemp > trigger_nevermore %}
            # nevermore is off and above trigger (this shouldn't happen)
            # enable nevermore
            SET_FAN_SPEED FAN=nevermore SPEED=1
        {% elif en_nevermore and chamberTemp < trigger_nevermore %}
            # nevermore is on and below trigger
            # disable nevermore and clear trigger
            SET_FAN_SPEED FAN=nevermore SPEED=0
            SET_GCODE_VARIABLE MACRO=HEAT_CHAMBER VARIABLE=trigger_nevermore VALUE=0
        {% elif chamberTemp < trigger_nevermore %}
            # below trigger; clear trigger (this shouldn't happen)
            SET_GCODE_VARIABLE MACRO=HEAT_CHAMBER VARIABLE=trigger_nevermore VALUE=0
        {% endif %}
        ## handle burner - cooling
        {% if en_burnerHeater %}
            # burner on; turn off w/fan on and reset cooldown
            SET_FAN_SPEED FAN=burnerHeater SPEED=0
            SET_FAN_SPEED FAN=burnerFan SPEED=1
            SET_GCODE_VARIABLE MACRO=HEAT_CHAMBER VARIABLE=burner_cooldown VALUE={ heat_chamber.burner_fan_delay }
        {% endif %}
        ## handle exhaust - cooling
        {% if not en_exhaust and chamberTemp > target_temp %}
            # exhaust is off and above target; turn on
            SET_FAN_SPEED FAN=exhaust SPEED=1
        {% elif en_exhaust and chamberTemp < target_temp %}
            # exhaust is on and below target; turn off
            SET_FAN_SPEED FAN=exhaust SPEED=0
        {% endif %}
    {% endif %}
    
    ## handle burner fan (independent of heating/cooling mode and chamber temp)
    {% if en_burnerHeater and not en_burnerFan %}
        # heater is on but fan is off (this shouldn't happen)
        # enable burner fan and reset cooldown
        SET_FAN_SPEED FAN=burnerFan SPEED=1
        SET_GCODE_VARIABLE MACRO=HEAT_CHAMBER VARIABLE=burner_cooldown VALUE={ heat_chamber.burner_fan_delay }
    {% elif not en_burnerHeater and en_burnerFan %}
        # heater is off but fan is on
        # check if cooldown done
        {% if (burner_cooldown - heat_chamber.check_interval) <= 0 %}
            # disable burner fan and clear cooldown
            SET_FAN_SPEED FAN=burnerFan SPEED=0
            SET_GCODE_VARIABLE MACRO=HEAT_CHAMBER VARIABLE=burner_cooldown VALUE=0
        # cooldown continues
        {% else %}
            # decrement burner cooldown
            SET_GCODE_VARIABLE MACRO=HEAT_CHAMBER VARIABLE=burner_cooldown VALUE={ burner_cooldown - heat_chamber.check_interval }
        {% endif %}
    {% endif %}

    ### decide if loop should continue (if any trigger still set)
    {% if trigger_nevermore > 0 or trigger_bedburner > 0 or trigger_exhaust > 0 %}
        # if still triggers, loop
        UPDATE_DELAYED_GCODE ID=chamber_monitor DURATION={ heat_chamber.check_interval }
    {% else %}
        m118 Chamber Monitor - End
        # if all clear, clear the mode
        SET_GCODE_VARIABLE MACRO=HEAT_CHAMBER VARIABLE=stage        VALUE="'None'"
        SET_GCODE_VARIABLE MACRO=HEAT_CHAMBER VARIABLE=target_temp  VALUE=0
    {% endif %}

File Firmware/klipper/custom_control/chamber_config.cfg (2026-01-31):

#####################################################################
#   Config - Filter
#####################################################################

[fan_generic nevermore]
pin: PB2
max_power: 1.0
min_power: 0.1
shutdown_speed: 0
cycle_time: 0.010
kick_start_time: 0.5

#####################################################################
#   Config - Chamber Temp and Exhaust
#####################################################################

[temperature_sensor chamber]
sensor_type: ATC Semitec 104NT-4-R025H42G
sensor_pin: PC1
min_temp: 10
max_temp: 100
gcode_id: C

[fan_generic exhaust]
pin: kpexp:PA1
max_power: 1.0
min_power: 0.1
shutdown_speed: 0
cycle_time: 0.010
kick_start_time: 0.5

#####################################################################
#   Config - BedBurner
#####################################################################

[fan_generic burnerFan]
pin: kpexp:PA2
max_power: 1.0
min_power: 0.1
shutdown_speed: 1
cycle_time: 0.010
kick_start_time: 0.5

[fan_generic burnerHeater]
pin: kpexp:PA3
max_power: 1.0
min_power: 0.1
shutdown_speed: 0
cycle_time: 0.100
kick_start_time: 0.100

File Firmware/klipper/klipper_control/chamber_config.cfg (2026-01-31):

#####################################################################
#   Config - Chamber Temp
#####################################################################

[temperature_sensor chamber]
sensor_type: ATC Semitec 104NT-4-R025H42G
sensor_pin: PC1
min_temp: 10
max_temp: 100
gcode_id: C

#####################################################################
#   Config - Filter and Exhaust
#####################################################################

[temperature_fan nevermore]
pin: PB2
max_power: 1.0
min_power: 0.1
shutdown_speed: 0
cycle_time: 0.010
kick_start_time: 0.5
sensor_type: temperature_combined
sensor_list: temperature_sensor chamber
combination_method: mean
maximum_deviation: 5
control: watermark
max_delta: 1.0
min_temp: 0
max_temp: 100
target_temp: 100.0

[temperature_fan exhaust]
pin: kpexp:PA1
max_power: 1.0
min_power: 0.1
shutdown_speed: 0
cycle_time: 0.010
kick_start_time: 0.5
sensor_type: temperature_combined
sensor_list: temperature_sensor chamber
combination_method: mean
maximum_deviation: 5
control: watermark
max_delta: 1.0
min_temp: 0
max_temp: 100
target_temp: 100.0

#####################################################################
#   Config - BedBurner
#####################################################################

[heater_generic bedBurner]
gcode_id: CX1
heater_pin: kpexp:PA3
max_power: 1.0
sensor_type: temperature_combined
sensor_list: temperature_sensor chamber
combination_method: mean
maximum_deviation: 5
control: watermark
max_delta: 0.5
min_temp: 0
max_temp: 100

[controller_fan bedBurnerFan]
pin: kpexp:PA2
max_power: 1.0
fan_speed: 1.0
shutdown_speed: 1.0
cycle_time: 0.010
kick_start_time: 0.5
idle_timeout: 30
stepper:
heater: bedBurner

[verify_heater bedBurner]
hysteresis: 100
check_gain_time: 600
heating_gain: 1

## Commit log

2026-01-24 readme bed height note
2026-01-24 block jigs
    [block_drill_guide.stl, block_router_template_ptc_1-16.stl, block_router_template_ptc_1-4.stl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]
2026-01-24 install spacers
    [install_spacer-block_deck.stl, install_spacer-block_frame.stl, install_spacer-duct_deck.stl]
2026-01-24 test setup
    [test_jig-duct_cover.stl, test_jig-spacer_deck.stl, test_jig-spacer_extrusion.stl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]
2026-01-24 fan duct stl
    [fan_duct.stl, fan_screw_spacer_x2.stl]
2026-01-24 test jig source
    [test_jig.FCStd]
2026-01-24 bracket and strap drawings
    [block_bracket_mildsteel16ga.dxf, block_bracket_mildsteel16ga_mirror.dxf, heater_strap_ptc.dxf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]
2026-01-24 klipper config
    [chamber_config.cfg, chamber_monitor.cfg]
2026-01-25 rename stl test jig to rig
    [test_rig-duct_cover.stl, test_rig-spacer_deck.stl, test_rig-spacer_extrusion.stl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]
2026-01-25 readme BOM
2026-01-25 Move full BOM into separate file
2026-01-27 refresh on strap dxf
    [bedburner-strap_ptc.dxf, bedburner-strap_tswitch.dxf]
2026-01-27 refresh on bracket step and dxf
    [bedburner-bracket_rear.dxf, bedburner-bracket_rear.step, block_bracket_mildsteel16ga.dxf]
2026-01-27 add block step
    [bedburner-block_ptc_tswitch.step]
2026-01-28 refresh block drill guides and router templates
    [block_drill_guide.stl, block_router_template_ptc_1-16.stl, block_router_template_ptc_1-4.stl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]
2026-01-29 longer ptc clearance and bracket techdraw refresh
    [bedburner-block_ptc_tswitch.step]
2026-01-30 rebuild assembly
    [bedburner-assembly.step, bedburner-block_ptc_tswitch.step, bedburner-bracket_rear.step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]
2026-01-30 refresh fan stl
    [fan_duct.stl, fan_screw_spacer_x2.stl]
2026-01-30 refresh guild and templates
    [block_drill_guide.stl, block_router_template_ptc_1-16.stl, block_router_template_ptc_1-8.stl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]
2026-01-30 add dxf for block machining and reorganize
    [bedburner-block_ptc_tswitch.dxf, bedburner-bracket_rear.dxf, bedburner-strap_ptc.dxf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]
2026-01-30 cad pictures
2026-01-31 software configuration documentation and examples
    [chamber_config.cfg, chamber_monitor.cfg]
2026-01-31 klipper macro fix
    [chamber_monitor.cfg]
2026-03-09 config readme
    I've tested the klipper control example enough. It's solid.
2026-04-12 freecad 1.1.0 recompute
    [bedburner.FCStd, test_jig.FCStd]
2026-04-12 Adding front heater bracket
    [bedburner-bracket_front.dxf, bedburner-bracket_front.step, bedburner.FCStd]
2026-04-12 added tfuse variant to block model and drill guides
    [bedburner-block_ptc_tfuse.step, bedburner.FCStd, block_drill_guide.stl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]
2026-04-12 add router templates for tfuse heater block
    regenerated other templates while at it
    [bedburner.FCStd, block_router_template_ptc_1-16.stl, block_router_template_ptc_1-8.stl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]
2026-04-12 add no pocket version of ptc tfuse block step file
    [bedburner-block_ptc_tfuse_no-pocket.step]
2026-04-12 bom readme reorganize
2026-06-03 fill in assembly readme
2026-06-03 assembly readme fix and formatting
2026-06-03 assembly readme formatting
2026-06-03 re-export heatsink dxf
    [bedburner-block_ptc_tfuse.dxf]
2026-06-03 add ptc tfuse block tech drawing
    [bedburner.FCStd]
